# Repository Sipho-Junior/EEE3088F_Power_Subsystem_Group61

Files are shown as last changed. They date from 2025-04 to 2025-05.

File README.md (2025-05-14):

# EEE3088F_Power_Subsystem_Group61 
The micro-mouse project requires the design and development of a compact, efficient, and reliable power subsystem capable of operating autonomously within a constrained embedded system.
This subsystem will be interfaced with the rest of the micro-mouse through a 2x16-pin header and a JST PH connector for the battery, designed to comply with the physical and electrical constraints specified in the project brief. 

This repository contains the design files and documentation for the power subsystem of an autonomous micro-mouse project developed for EEE3088F 2025. The micro-mouse is designed to navigate and solve mazes autonomously.

# System Architecture
The complete micro-mouse consists of four essential subsystems:

Motherboard - The foundation PCB connecting all other components
Processor Board - Features an STM32L476 microcontroller for computation and control
Sensing Subsystem - Equipped with distance sensors for environmental awareness
Power Subsystem - Focus of this repository

# Power Subsystem Features
The power subsystem is responsible for:

Providing stable 3.3V and 5V power to all micro-mouse components
Controlling up to 4 motors bidirectionally (2 main motors + 2 auxiliary)
Supporting external load switching (2 channels at 1A each)
Real-time power monitoring via INA219 on I2C bus
Battery management for a 1S1P LiPo battery (800mAh 3.7V)
Dual charging modes (200mA and 600mA±100mA)
USB-C power input with 9V Power Delivery negotiation
Power system ON/OFF control with ultra-low standby current (<30μA)

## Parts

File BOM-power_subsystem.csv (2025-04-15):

Comment | Designator | Footprint | LCSC | Quantity
SW_Nidec_CAS-120A1 | SW2 | Nidec_Copal_CAS-120A | C115374 | 1
22u | C12 | C_0201_0603Metric | C12891 | 1
INA219AxD | U3 | SOIC-8_3.9x4.9mm_P1.27mm | C138706 | 1
10k | R13,R24,R6,R7 | R_0201_0603Metric | C17414 | 4
6.8K | R12,R8,R9 | R_0201_0603Metric | C17772 | 3
4.7u | C14,C15 | C_0201_0603Metric | C1779 | 2
74K | R14 | R_0201_0603Metric | C17801 | 1
100k | R10,R11 | R_0201_0603Metric | C17900 | 2
4450 | R23,R25 | R_0201_0603Metric | C1980 | 2
NPN | Q1 | TO-92L_HandSolder | C2145 | 1
LED | D1 | LED_0201_0603Metric | C2296 | 1
LED | D2 | LED_0201_0603Metric | C2297 | 1
PMOS | Q2,Q3 | TO-92L_Inline | C2564 | 2
0.01u | C6,C7 | C_0201_0603Metric | C38523 | 2
USB_C_Receptacle_PowerOnly_6P | J3 | USB_C_Receptacle_GCT_USB4125-xx-x-0190_6P_TopMnt_Horizontal | C399924 | 1
2K | R19,R20 | R_0201_0603Metric | C4109 | 2
1.8k | R26 | R_0201_0603Metric | C4177 | 1
1640 | R16,R22 | R_0201_0603Metric | C4310 | 2
1k | R15,R21,R4,R5 | R_0201_0603Metric | C4410 | 4
22u | C4,C5 | C_0201_0603Metric | C45783 | 2
AMS1117-3.3 | U7 | SOT-223-3_TabPin2 | C5120796 | 1
BQ24074RGT | U4 | VQFN-16-1EP_3x3mm_P0.5mm_EP1.8x1.8mm | C54313 | 1
DRV8833PW | U1,U6 | TSSOP-16_4.4x5mm_P0.65mm | C544801 | 2
10u | C10,C11,C13,C3,C8,C9 | C_0201_0603Metric | C7171 | 6
MT3608 | U5 | SOT-23-6 | C84817 | 1
CH224K | U2 | SSOP-10-1EP_3.9x4.9mm_P1mm_EP2.1x3.3mm | C970725 | 1

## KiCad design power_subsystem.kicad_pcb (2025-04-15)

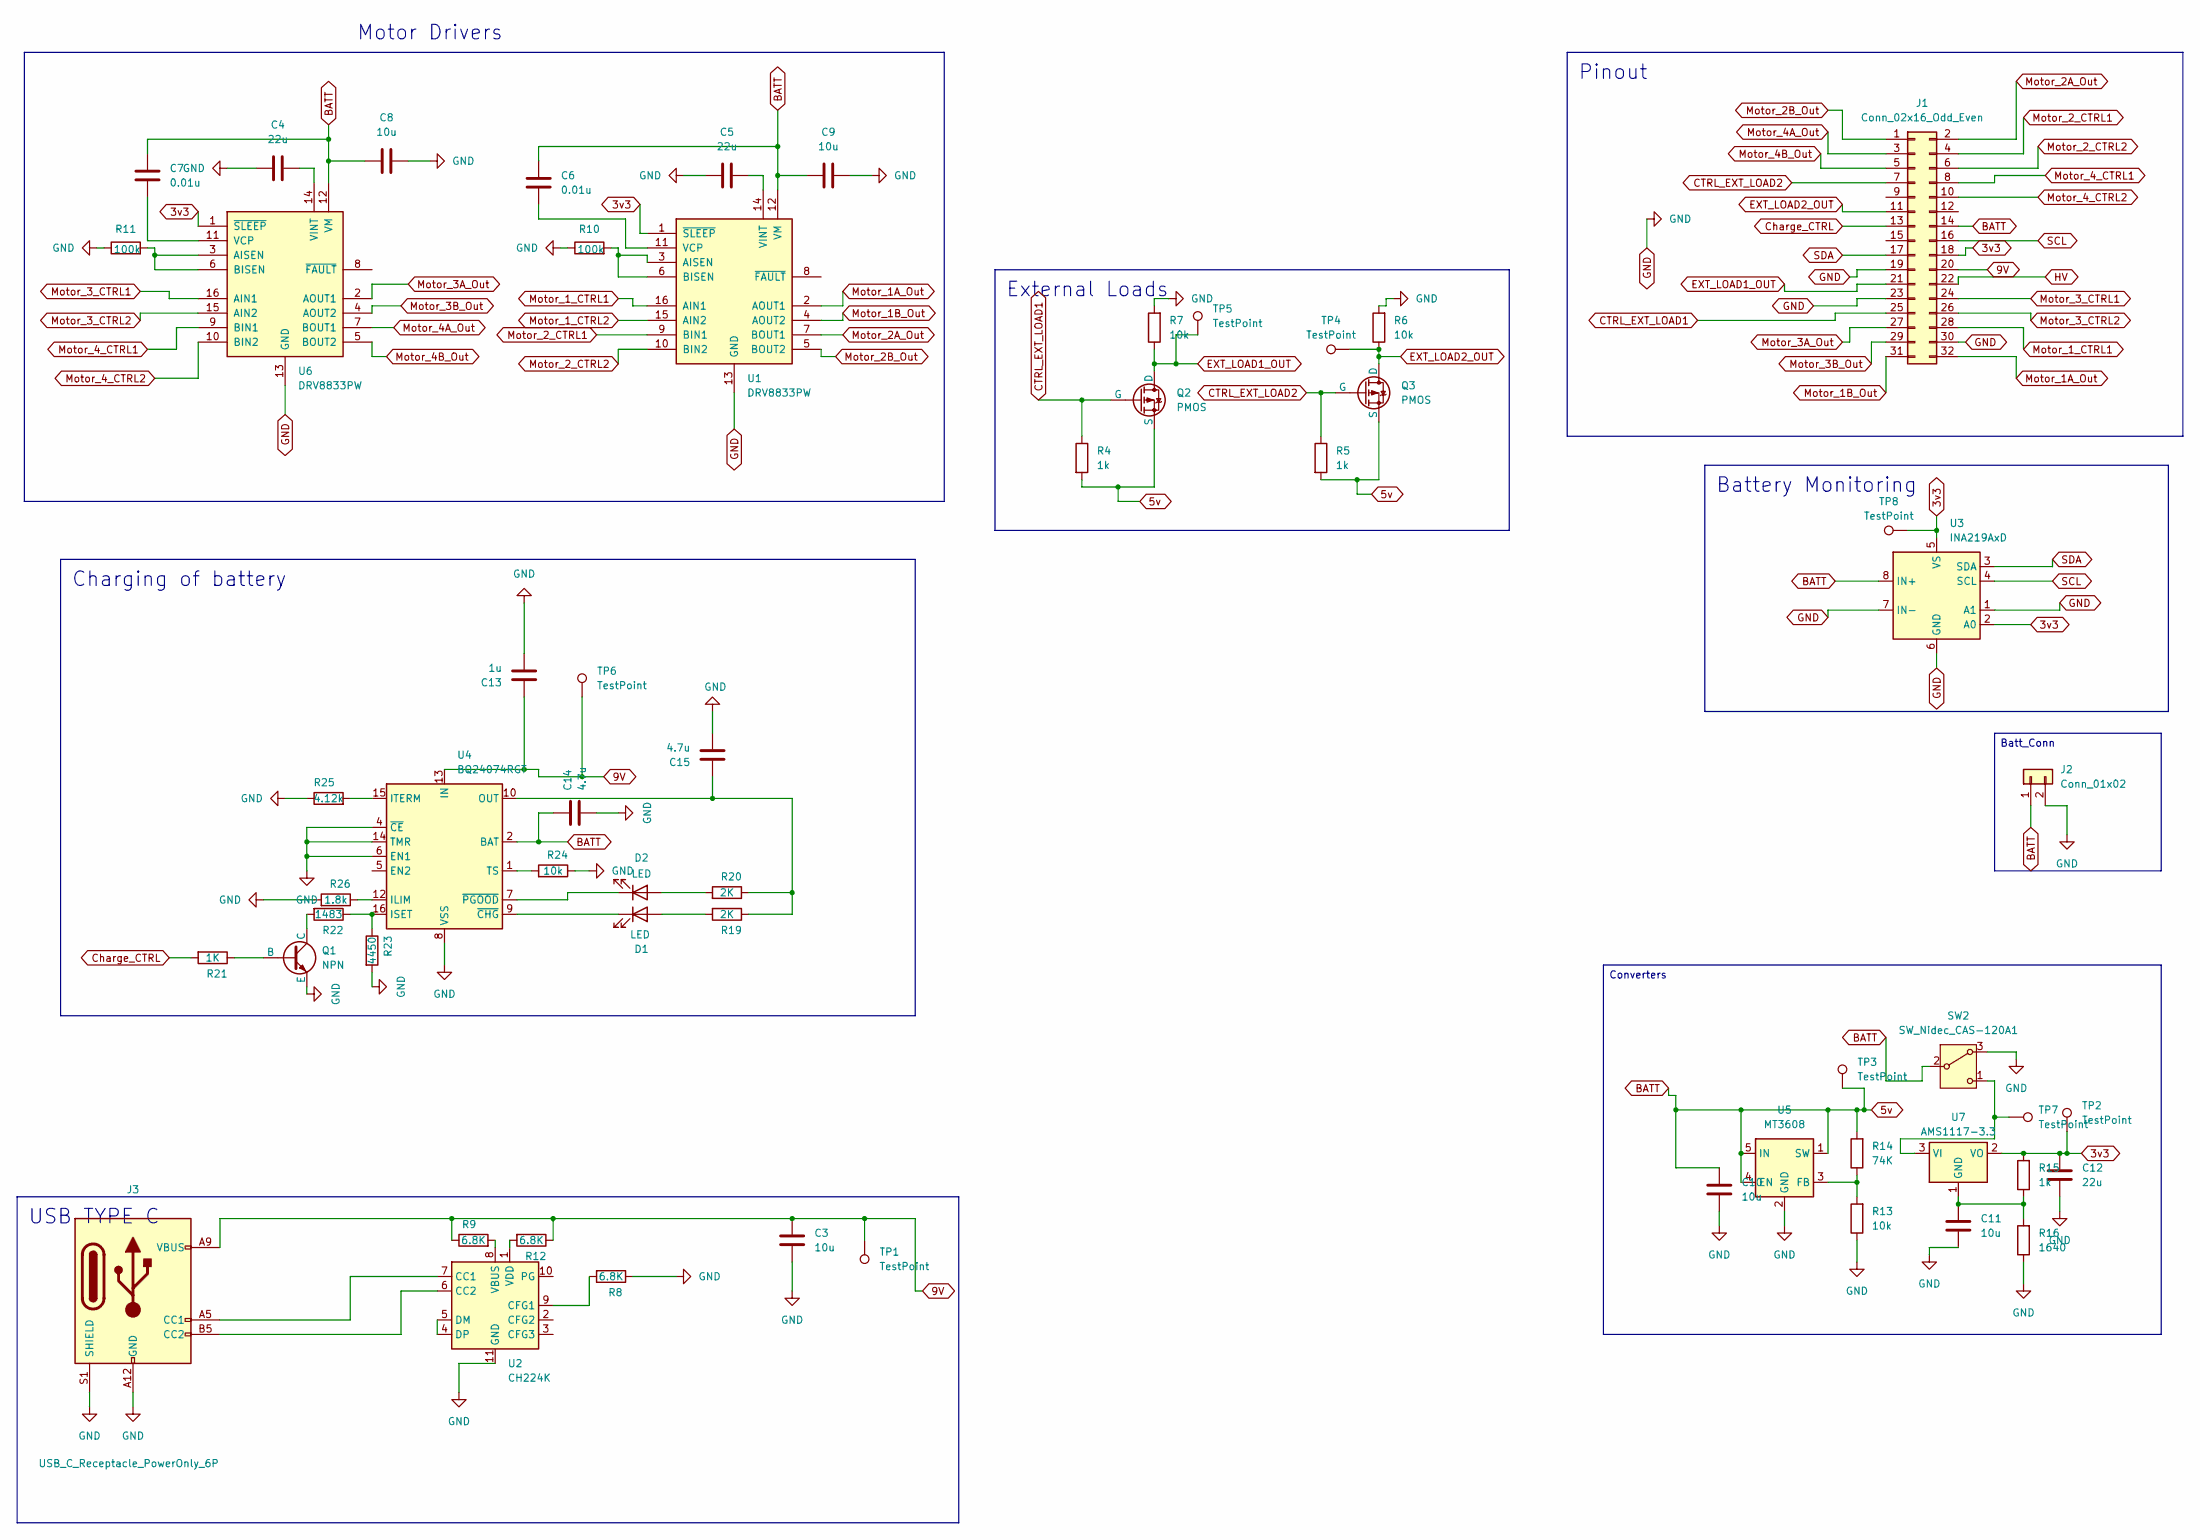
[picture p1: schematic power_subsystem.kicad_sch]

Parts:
C3, C8, C9, C10, C11: 10u; C_0201_0603Metric
C4, C5, C12: 22u; C_0201_0603Metric
C6, C7: 0.01u; C_0201_0603Metric
C13: 1u; C_0201_0603Metric
C14, C15: 4.7u; C_0201_0603Metric
D1, D2: LED; LED_0201_0603Metric
J1: Conn_02x16_Odd_Even; PinHeader_2x16_P2.54mm_Vertical
J2: Conn_01x02; JST_PH_S2B-PH-K_1x02_P2.00mm_Horizontal
J3: USB_C_Receptacle_PowerOnly_6P; USB_C_Receptacle_GCT_USB4125-xx-x-0190_6P_TopMnt_Horizontal
Q1: NPN; TO-92L_HandSolder
Q2, Q3: PMOS; TO-92L_Inline
R4, R5, R15: 1k; R_0201_0603Metric
R6, R7, R13, R24: 10k; R_0201_0603Metric
R8, R9, R12: 6.8K; R_0201_0603Metric
R10, R11: 100k; R_0201_0603Metric
R14: 74K; R_0201_0603Metric
R16: 1640; R_0201_0603Metric
R19, R20: 2K; R_0201_0603Metric
R21: 1K; R_0201_0603Metric
R22: 1483; R_0201_0603Metric
R23: 4450; R_0201_0603Metric
R25: 4.12k; R_0201_0603Metric
R26: 1.8k; R_0201_0603Metric
SW2: SW_Nidec_CAS-120A1; Nidec_Copal_CAS-120A
TP1, TP2, TP3, TP4, TP5, TP6, TP7, TP8: TestPoint; TestPoint_Pad_D1.5mm
U1, U6: DRV8833PW; TSSOP-16_4.4x5mm_P0.65mm
U2: CH224K; SSOP-10-1EP_3.9x4.9mm_P1mm_EP2.1x3.3mm
U3: INA219AxD; SOIC-8_3.9x4.9mm_P1.27mm
U4: BQ24074RGT; VQFN-16-1EP_3x3mm_P0.5mm_EP1.8x1.8mm
U5: MT3608; SOT-23-6
U7: AMS1117-3.3; SOT-223-3_TabPin2

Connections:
3v3: C12.2, J1.18, R15.2, TP2.1, TP8.1, U1.1 (~SLEEP), U3.2 (A0), U3.5 (VS), U6.1 (~SLEEP), U7.2 (VO)
5v: C6.1, C7.1, C8.1, C9.1, C10.2, C14.2, J1.14, J2.1, Q2.3 (S), Q3.3 (S), R4.2, R5.2, R14.2, SW2.2 (B), TP3.1, U1.12 (VM), U3.8 (IN+), U4.2 (BAT), U4.3 (BAT), U5.1 (SW), U5.4 (EN), U5.5 (IN), U6.12 (VM)
9V: C3.2, C13.2, J1.20, J3.A9 (VBUS), J3.B9 (VBUS), R9.1, R12.1, TP1.1, TP6.1, U4.13 (IN)
CTRL_EXT_LOAD1: J1.25, Q2.2 (G), R4.1
CTRL_EXT_LOAD2: J1.7, Q3.2 (G), R5.1
Charge_CTRL: J1.13, R21.2
EXT_LOAD1_OUT: J1.21, Q2.1 (D), R7.1, TP5.1
EXT_LOAD2_OUT: J1.11, Q3.1 (D), R6.1, TP4.1
GND: C3.1, C4.1, C5.1, C8.2, C9.2, C10.1, C11.1, C12.1, C13.1, C14.1, C15.1, J1.19, J1.23, J1.30, J2.2, J3.A12 (GND), J3.B12 (GND), J3.S1 (SHIELD), Q1.3 (E), R6.2, R7.2, R8.1, R10.1, R11.1, R13.1, R16.1, R23.2, R24.1, R25.1, R26.2, SW2.3 (A), U1.13 (GND), U2.11 (GND), U3.1 (A1), U3.6 (GND), U3.7 (IN-), U4.4 (~CE), U4.6 (EN1), U4.8 (VSS), U4.14 (TMR), U4.17 (VSS), U5.2 (GND), U6.13 (GND)
HV: J1.22
Motor_1A_Out: J1.32, U1.2 (AOUT1)
Motor_1B_Out: J1.31, U1.4 (AOUT2)
Motor_1_CTRL1: J1.28, U1.16 (AIN1)
Motor_1_CTRL2: U1.15 (AIN2)
Motor_2A_Out: J1.2, U1.7 (BOUT1)
Motor_2B_Out: J1.1, U1.5 (BOUT2)
Motor_2_CTRL1: J1.4, U1.9 (BIN1)
Motor_2_CTRL2: J1.6, U1.10 (BIN2)
Motor_3A_Out: J1.27, U6.2 (AOUT1)
Motor_3B_Out: J1.29, U6.4 (AOUT2)
Motor_3_CTRL1: J1.24, U6.16 (AIN1)
Motor_3_CTRL2: J1.26, U6.15 (AIN2)
Motor_4A_Out: J1.3, U6.7 (BOUT1)
Motor_4B_Out: J1.5, U6.5 (BOUT2)
Motor_4_CTRL1: J1.8, U6.9 (BIN1)
Motor_4_CTRL2: J1.10, U6.10 (BIN2)
unnamed: C15.2, R19.1, R20.1, U4.10 (OUT), U4.11 (OUT)
unnamed: D1.2 (A), R19.2
unnamed: D1.1 (K), U4.9 (~CHG)
unnamed: D2.2 (A), R20.2
unnamed: D2.1 (K), U4.7 (~PGOOD)
unnamed: J3.A5 (CC1), U2.7 (CC1)
unnamed: J3.B5 (CC2), U2.6 (CC2)
unnamed: Q1.2 (B), R21.1
unnamed: Q1.1 (C), R22.2
unnamed: SW2.1 (C), TP7.1, U7.3 (VI)
unnamed: R10.2, U1.3 (AISEN), U1.6 (BISEN)
unnamed: C6.2, U1.11 (VCP)
unnamed: C5.2, U1.14 (VINT)
unnamed: R8.2, U2.9 (CFG1)
unnamed: U2.4 (DP), U2.5 (DM)
unnamed: R9.2, U2.8 (VBUS)
unnamed: R12.2, U2.1 (VDD)
unnamed: R26.1, U4.12 (ILIM)
unnamed: R22.1, R23.1, U4.16 (ISET)
unnamed: R25.2, U4.15 (ITERM)
unnamed: R24.2, U4.1 (TS)
unnamed: R13.2, R14.1, U5.3 (FB)
unnamed: R11.2, U6.3 (AISEN), U6.6 (BISEN)
unnamed: C7.2, U6.11 (VCP)
unnamed: C4.2, U6.14 (VINT)
unnamed: C11.2, R15.1, R16.2, U7.1 (GND)
SCL: J1.16, U3.4 (SCL)
SDA: J1.17, U3.3 (SDA)

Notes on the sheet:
Motor Drivers
Converters
USB TYPE C
Charging of battery
Pinout
External Loads
Battery Monitoring
Batt_Conn

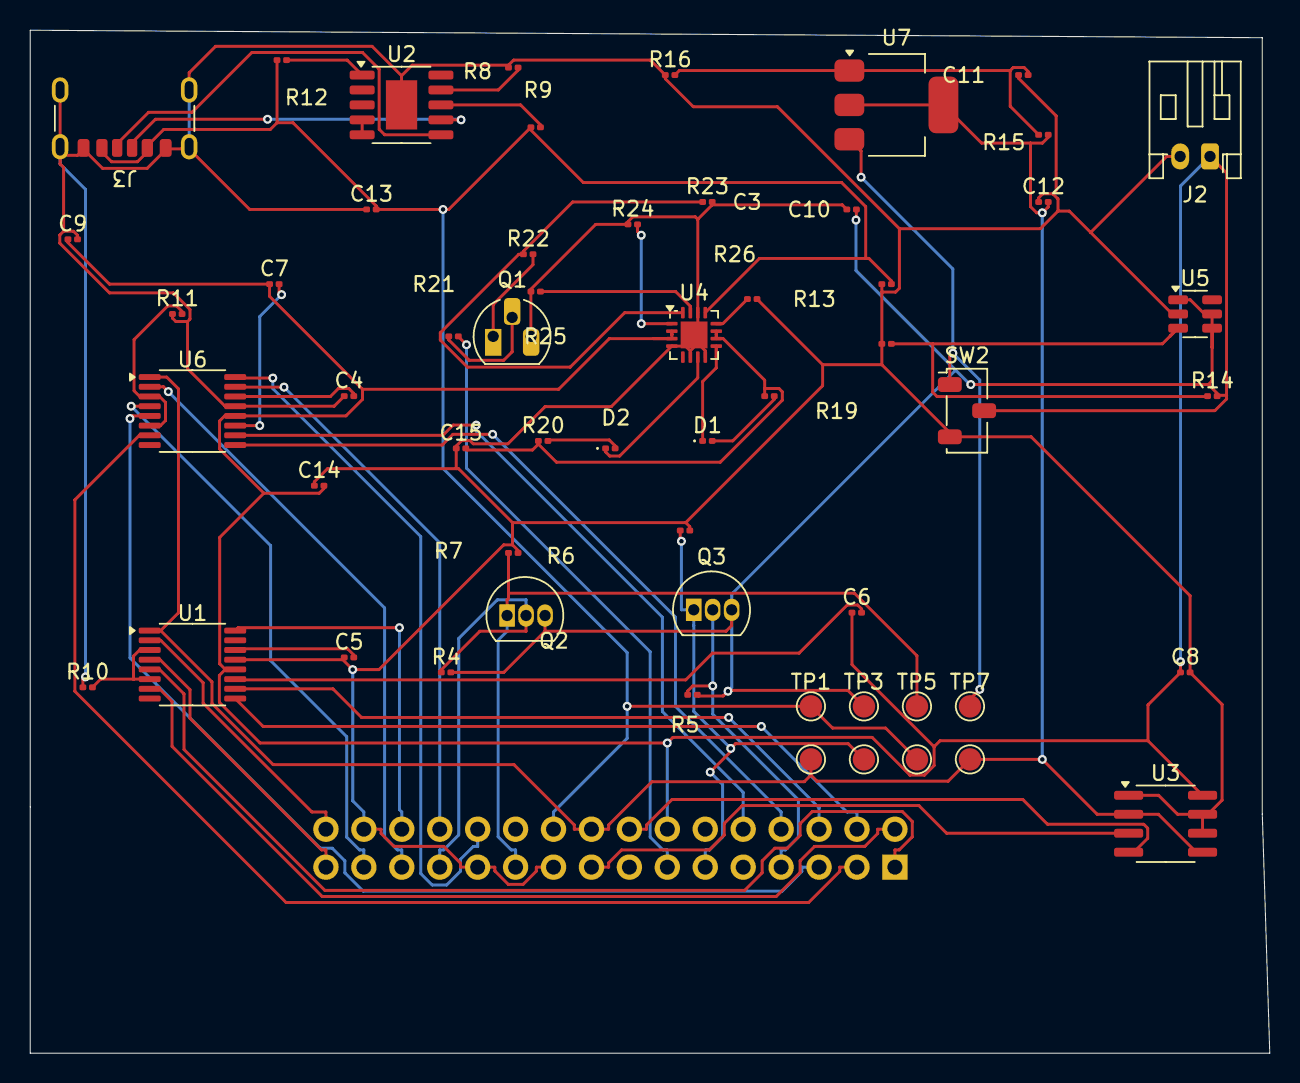
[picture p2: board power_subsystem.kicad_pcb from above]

Board: 2 copper layers, 83.0 x 68.5 mm, 58 parts (1 on the bottom side), 52 nets.
